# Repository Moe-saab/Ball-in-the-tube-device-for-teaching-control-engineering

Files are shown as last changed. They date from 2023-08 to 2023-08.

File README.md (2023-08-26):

# Ball-in-the-tube-device-for-teaching-control-engineering
Demo here : https://youtu.be/UmyqPj7e6xY  
Goal is to make the ball inside the tube track a given reference position or group of reference positions, by designing a controller.  
Using linear control theory, identification, model verification, and finally control is done on the ball in the tube system. In addition to that cascaded control is done results in very high agreement between controlled model and controlled real system.  
In the given software, you are free to use only system as a whole to implement a controller based on a direct model from the motor input voltage (duty cycle input) to the output distance measured from the infrared sensor.  
If you want to improve the control, use cascaded control. For this use the ball subsystem and motor subsystem folders.  
You can use or share any part of this work.  

The stl files are from mathworks , thanks to Brian McKay.  
System:
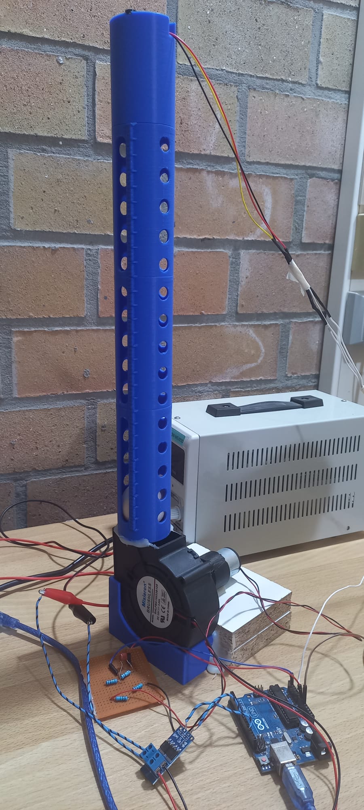
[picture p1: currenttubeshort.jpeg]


Results for motor control
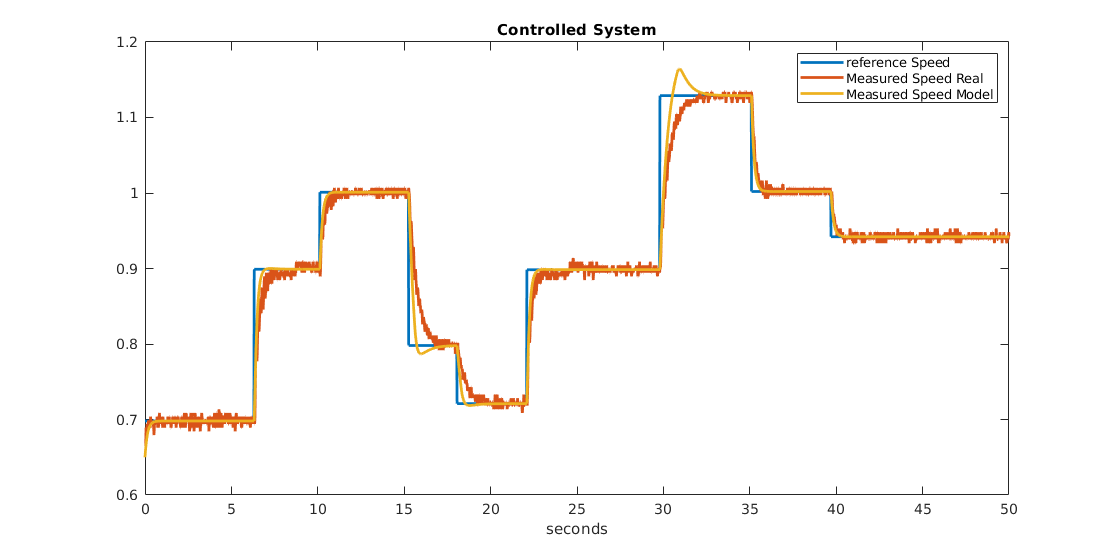
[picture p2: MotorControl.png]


Results for ball position control
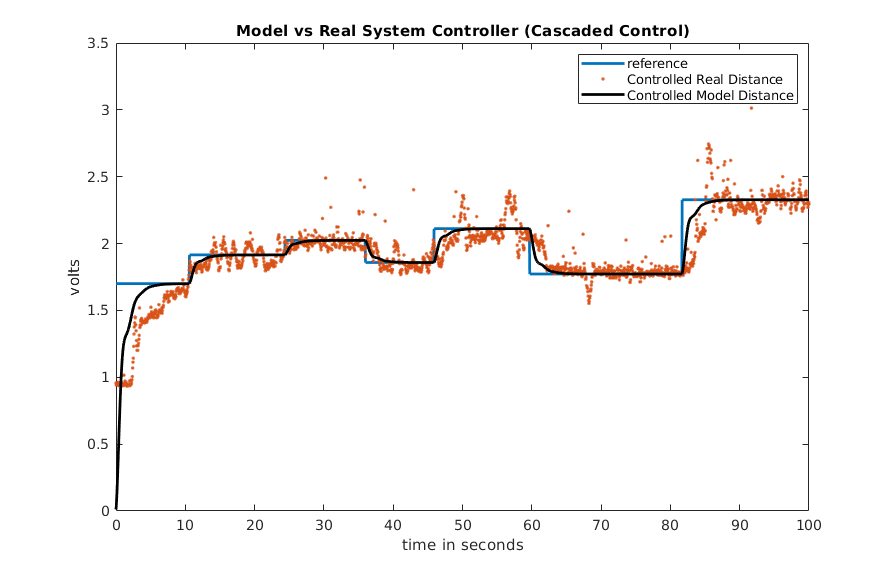
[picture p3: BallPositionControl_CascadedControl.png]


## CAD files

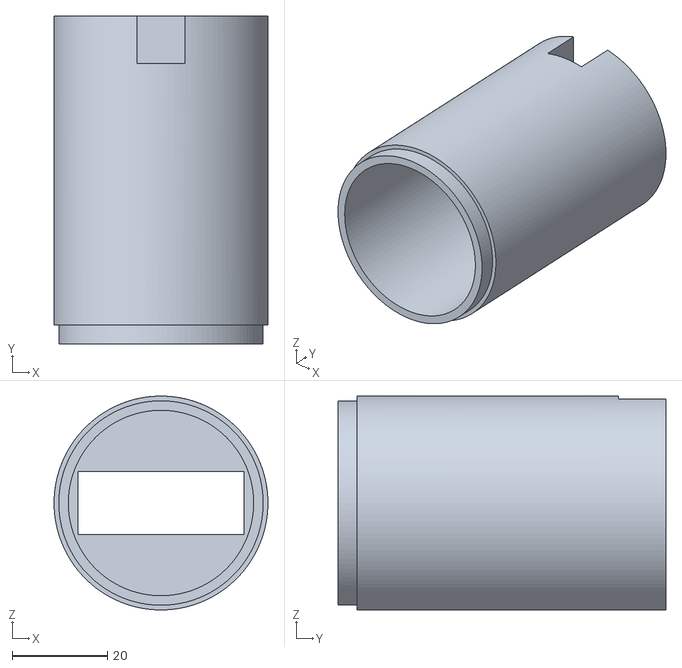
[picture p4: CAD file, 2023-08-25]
tube_cap.stl
45.0 x 69.0 x 45.0

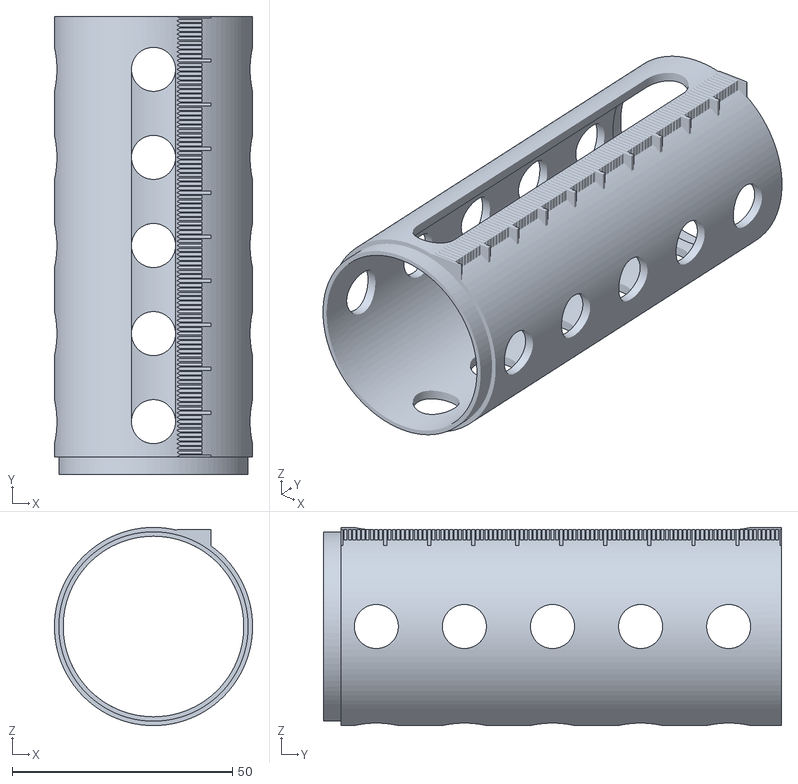
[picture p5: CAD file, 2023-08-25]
tube_center.stl
45.0 x 104.0 x 45.0

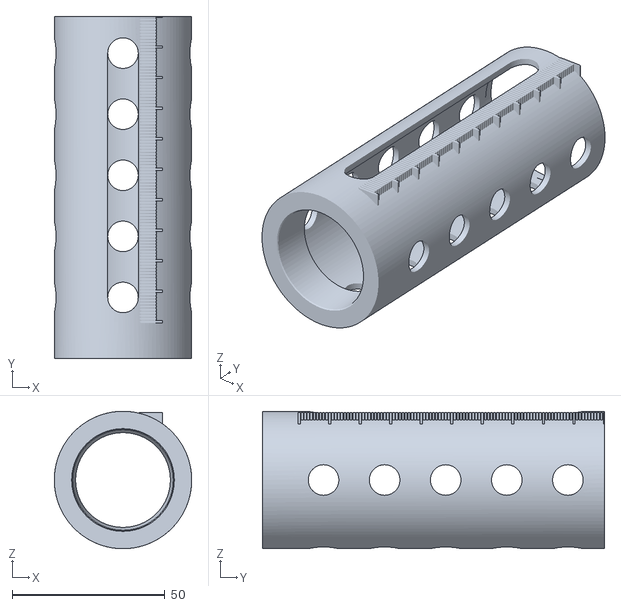
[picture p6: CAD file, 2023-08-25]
tube_bottom.stl
45.0 x 112.0 x 45.0

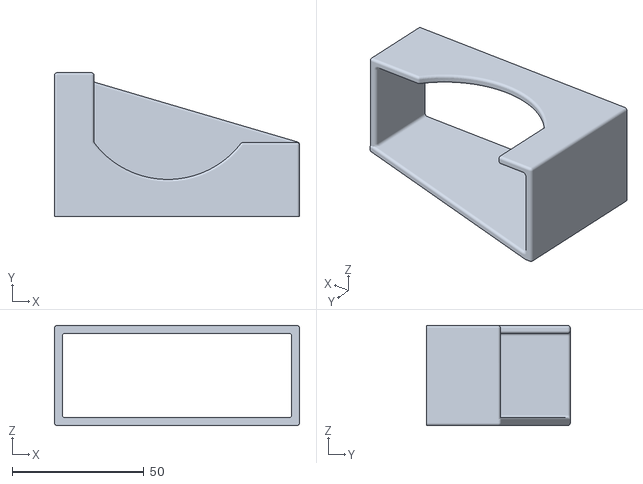
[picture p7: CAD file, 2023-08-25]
fan_holder.stl
93.0 x 54.5 x 38.0

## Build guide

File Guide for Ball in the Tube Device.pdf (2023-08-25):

## Guide for Ball in the Tube Device

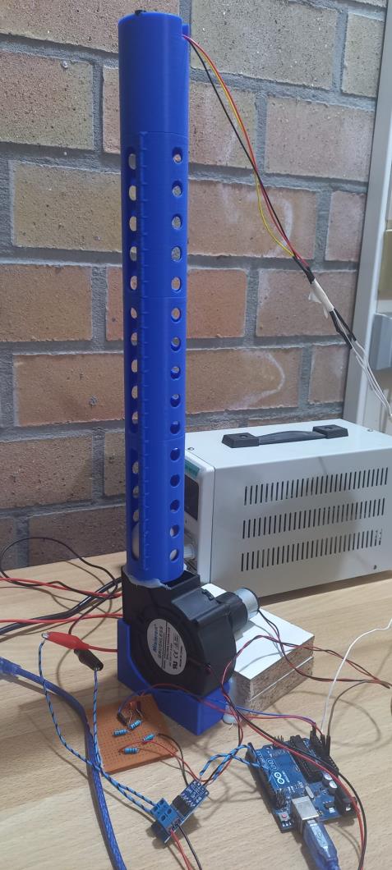
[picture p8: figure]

A. Hardware Required
a. Power Supply 7.5 volts with at least 2 amp current
b. Arduino Uno
c. 1/11 Voltage divider circuit – 2 Resistors were used 1Mega ohm and 100k ohm, in addition a 1 nano farad capacitor is recommended.
d. MOSFET Switch Modules Amazon Link (https://www.amazon.com.be/gp/product/B09SV2LT3B/ref=ppx_yo_dt_b_asin_title_o03_s00?ie=UTF8&psc=1)
e. Short Range Sharp Infrared Sensor GP2Y0A41SK0F Amazon Link (https://www.amazon.com.be/-/en/GP2Y0A41SK0F-Infrared-Telemetry-Measuring-Distance/dp/B096ZXY5JM?s=industrial)
f. 3d printed tube Download Here (https://github.com/Moe-saab/Ball-in-the-tube-device-for-teaching-control-engineering)
g. DC motor acting as a generator to be coupled with the major brushless fan for speed measurement.
h. Brushless dc fan Amazon Link (https://www.amazon.com.be/-/en/Radial-Brushless-Bearing-Cooling-Centrifugal/dp/B08WR1Q9M7?hvadid=633420129017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)
i. Ping Pong Ball

j. Wires
k. Separate Power Supply for infrared sensor (5 Volt). Don’t use the Arduino 5volt port as it will cause noise for the motor speed readings.
B. Setup
a. Use Arduino pin 9 for pwm output to the mosfet switch module. Don’t use other pins as some are not capable of giving pwm signal, and some can but with lower frequency.
b. Use common ground for all system, connect ground of power supply of the fan, generator, and infrared sensor together with the Arduino ground pin.
c. Center the tube over the direct airflow section of the fan, the fix it using hot glue or 3d print a mount optionally.
C. Software
a. Use arduino toolbox for matlab Link (https://nl.mathworks.com/hardware-support/arduino.html#matlab)
b. If using linux, need to give read and write permission to the arduino before starting matlab, use this command : sudo chmod a+rw /dev/ttyACM0
c. If using windows computer, replace in all the software provided the line connecting to arduino with this: a = arduino('com3','uno');
d. Use the following link for reference of software implemented : Github Link (https://github.com/Moe-saab/Ball-in-the-tube-device-for-teaching-control-engineering)
